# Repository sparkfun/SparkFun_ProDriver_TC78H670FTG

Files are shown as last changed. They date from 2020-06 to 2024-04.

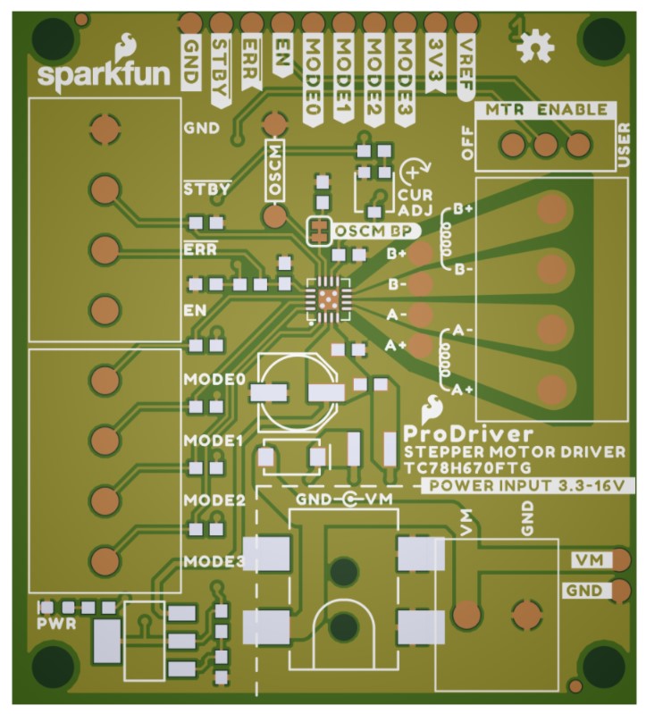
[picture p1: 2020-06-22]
Documents/brd_top_preivew.jpg

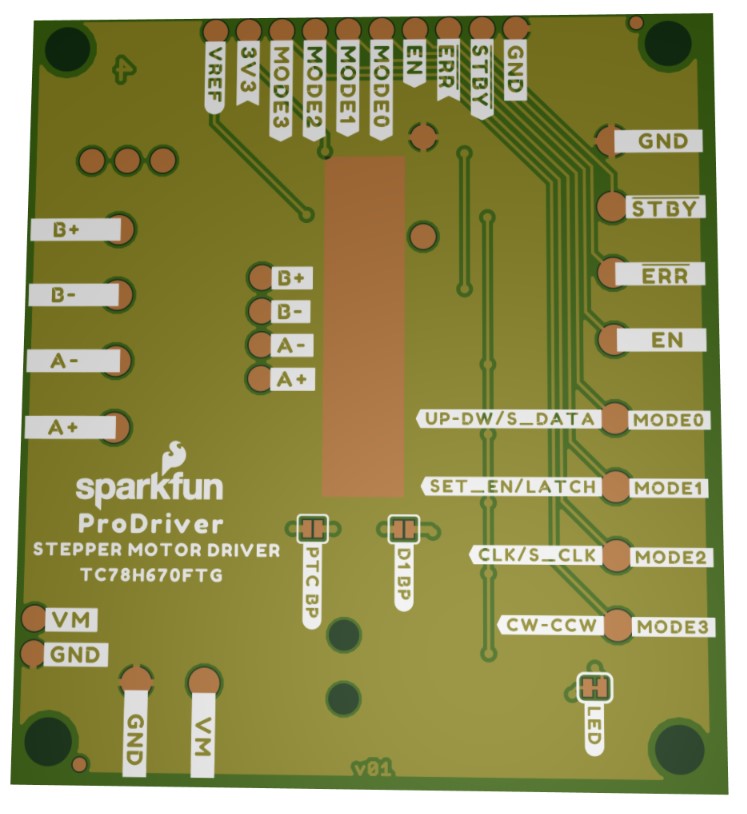
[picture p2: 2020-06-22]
Documents/brd_bottom_preivew.jpg

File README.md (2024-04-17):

SparkFun ProDriver - Stepper Motor Driver (TC78H670FTG)
========================================

SparkFun ProDriver - Stepper Motor Driver (TC78H670FTG)

[*SparkFun ProDriver - Stepper Motor Driver (TC78H670FTG) (ROB-16836)*](https://www.sparkfun.com/products/16836)

The SparkFun ProDriver makes it easy to start developing with the TC78H670FTG bipolar stepper motor driver from Toshiba! Latch terminals provide instant solder-less connections to every feature offered. Use our extensive Arduino Library with 10 examples, and you can quickly explore the many features of this precise and small package size motor driver IC.

In addition to high resolution control (down to 1/128th of a step), the ProDriver can be controlled via traditional clock-in stepping or serial commands. Both methods are demonstrated in the Arduino Library. The serial command method is especially unique in that it allows the user to precisely control the phase, torque, current limit and mixed decay ratio of each coil immediately during stepping. Most stepper motor driver ICs require using an external trimpot to set the current limit, but with the ProDriver, you can precisely adjust this via serial commands!

Repository Contents
-------------------

* **/Documentation** - Datasheets, additional product information
* **/Hardware** - Eagle design files (.brd, .sch)
* **/Hardware/Production** - Production panel files and gerbers (.brd)

Documentation
--------------

* **[Hookup Guide](https://learn.sparkfun.com/tutorials/1200)** - A hookup guide for the SparkFun ProDriver and Mini Stepper Motor Driver (TC78H670FTG)
* **[Arduino Library](https://github.com/sparkfun/SparkFun_ProDriver_TC78H670FTG_Arduino_Library)** - Basic Arduino Library for the SparkFun ProDriver and Mini Stepper Motor Driver (TC78H670FTG)

Product Variants
----------------
* SparkFun Mini Stepper Motor Driver - TC78H670FTG
  * [ROB-25167](https://www.sparkfun.com/products/25167)- v1.0, Initial Release
* SparkFun ProDriver - Stepper Motor Driver (TC78H670FTG)
  * [ROB-16836](https://www.sparkfun.com/products/16836)- v1.0, Initial Release

Product Versions
----------------
* [v01](https://github.com/sparkfun/SparkFun_ProDriver_TC78H670FTG/releases/tag/v10) - Initial Release

License Information
-------------------

This product is _**open source**_!

Please review the LICENSE.md file for license information.

If you have any questions or concerns on licensing, please contact technical support on our [SparkFun forums](https://forum.sparkfun.com/viewforum.php?f=152).

Distributed as-is; no warranty is given.

- Your friends at SparkFun.

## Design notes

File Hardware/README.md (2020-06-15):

SparkFun Particle Sensor MAX30101 (Qwiic) Design Files
=====================================

The .sch and .brd files hare are Eagle CAD schematic and PCB design files from SparkFun Electronics.
A freeware version of Eagle can be found [here](https://www.autodesk.com/products/eagle/free-download).

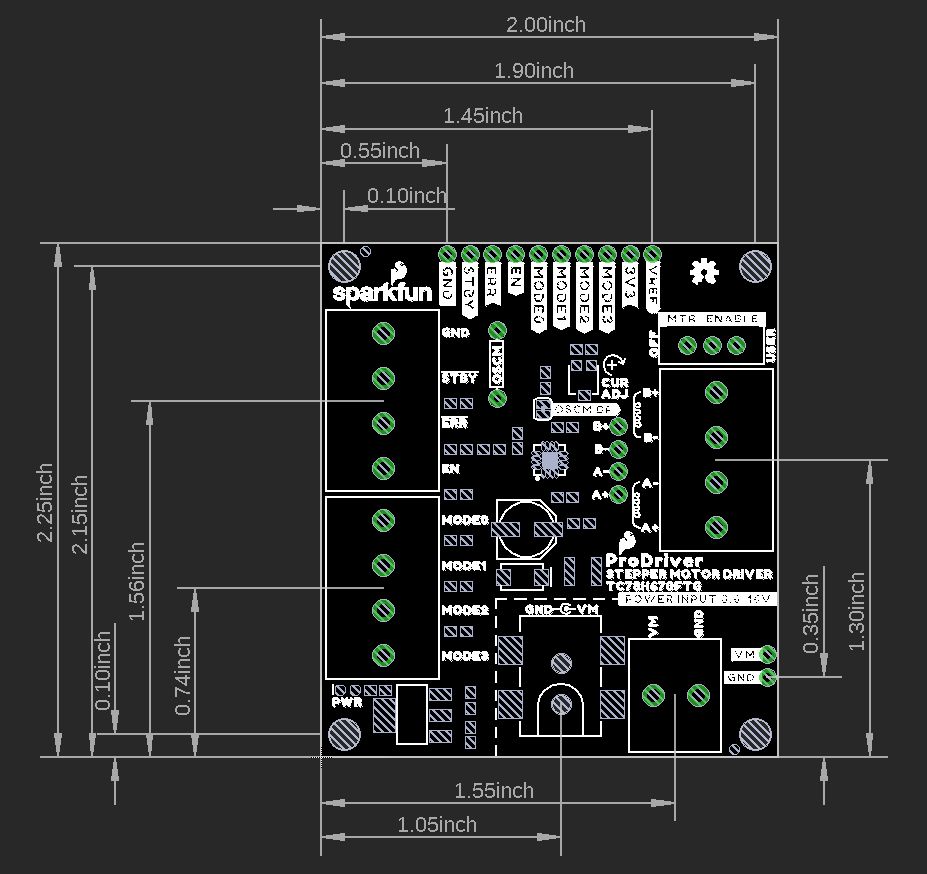
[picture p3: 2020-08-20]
Documents/SparkFun_ProDriver_DIMENSIONAL.png

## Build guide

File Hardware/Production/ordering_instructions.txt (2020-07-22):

panel size, 116x180mm
PCB thickness, 1.6mm
number of layers, 4
soldermask color, Red
silkscreen color, White
oz copper, 1oz
finish, HASL lead free
stencils, top+bottom
pcs per panel, 6
min trace width, 0.2032mm / 0.0080in
min drill size, 0.3048mm / 0.0120in
filename to layer stackup 1/2/3/4: GTL, GL2, GL3, GBL

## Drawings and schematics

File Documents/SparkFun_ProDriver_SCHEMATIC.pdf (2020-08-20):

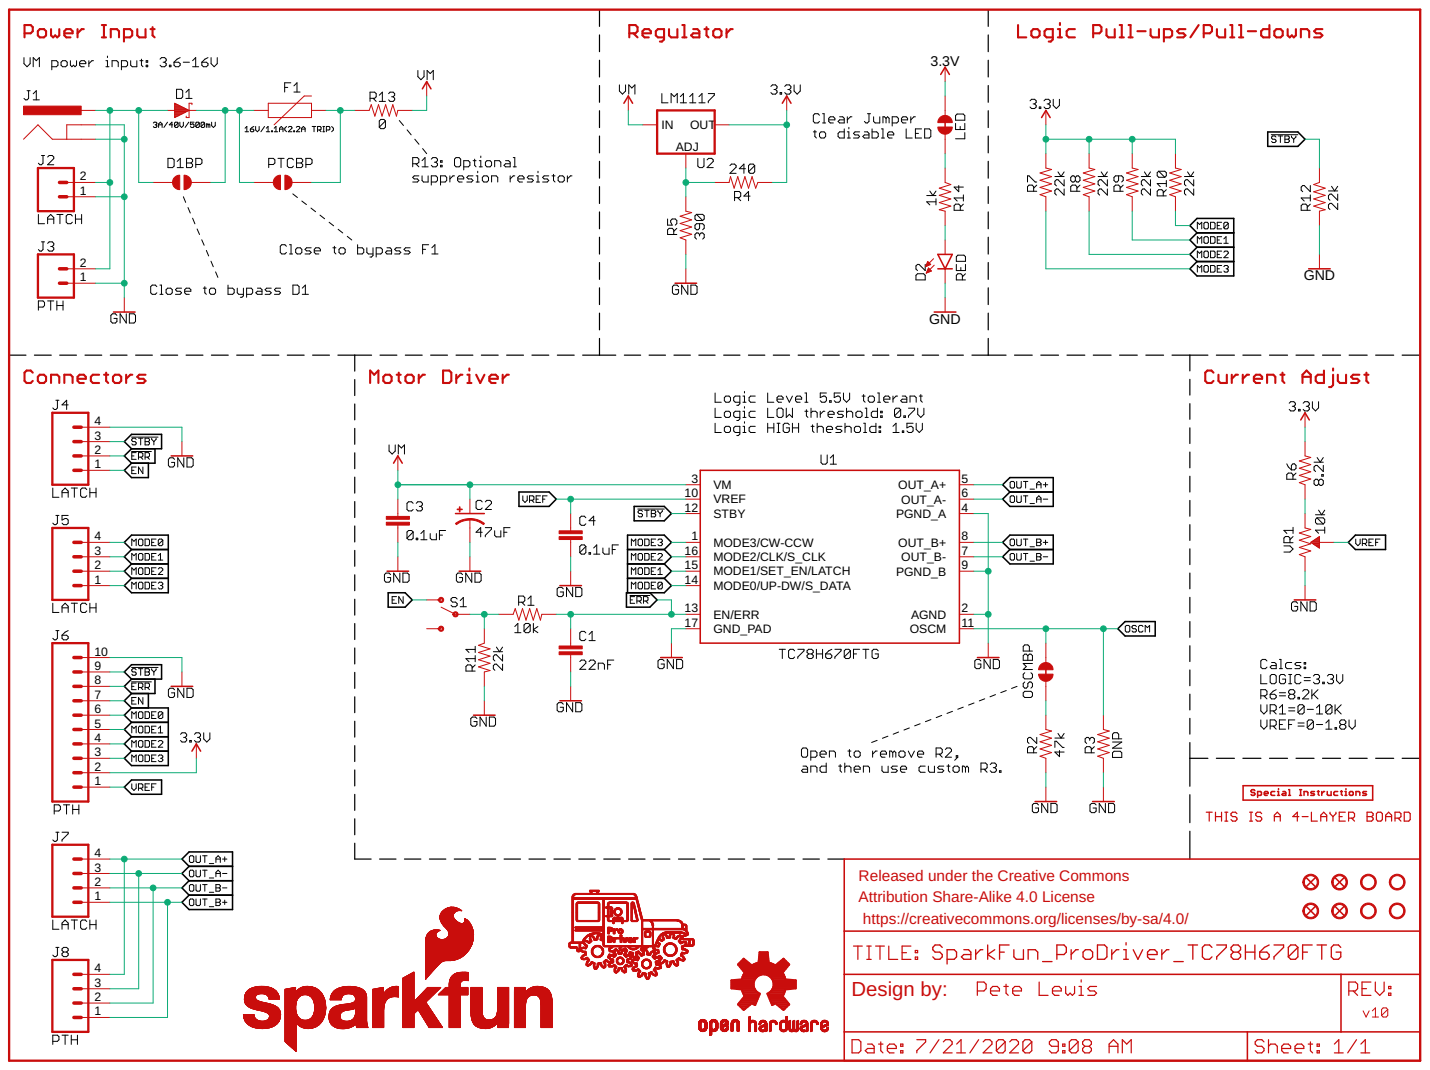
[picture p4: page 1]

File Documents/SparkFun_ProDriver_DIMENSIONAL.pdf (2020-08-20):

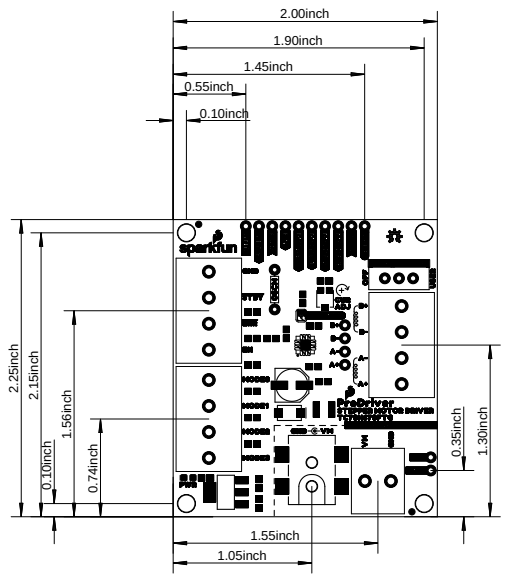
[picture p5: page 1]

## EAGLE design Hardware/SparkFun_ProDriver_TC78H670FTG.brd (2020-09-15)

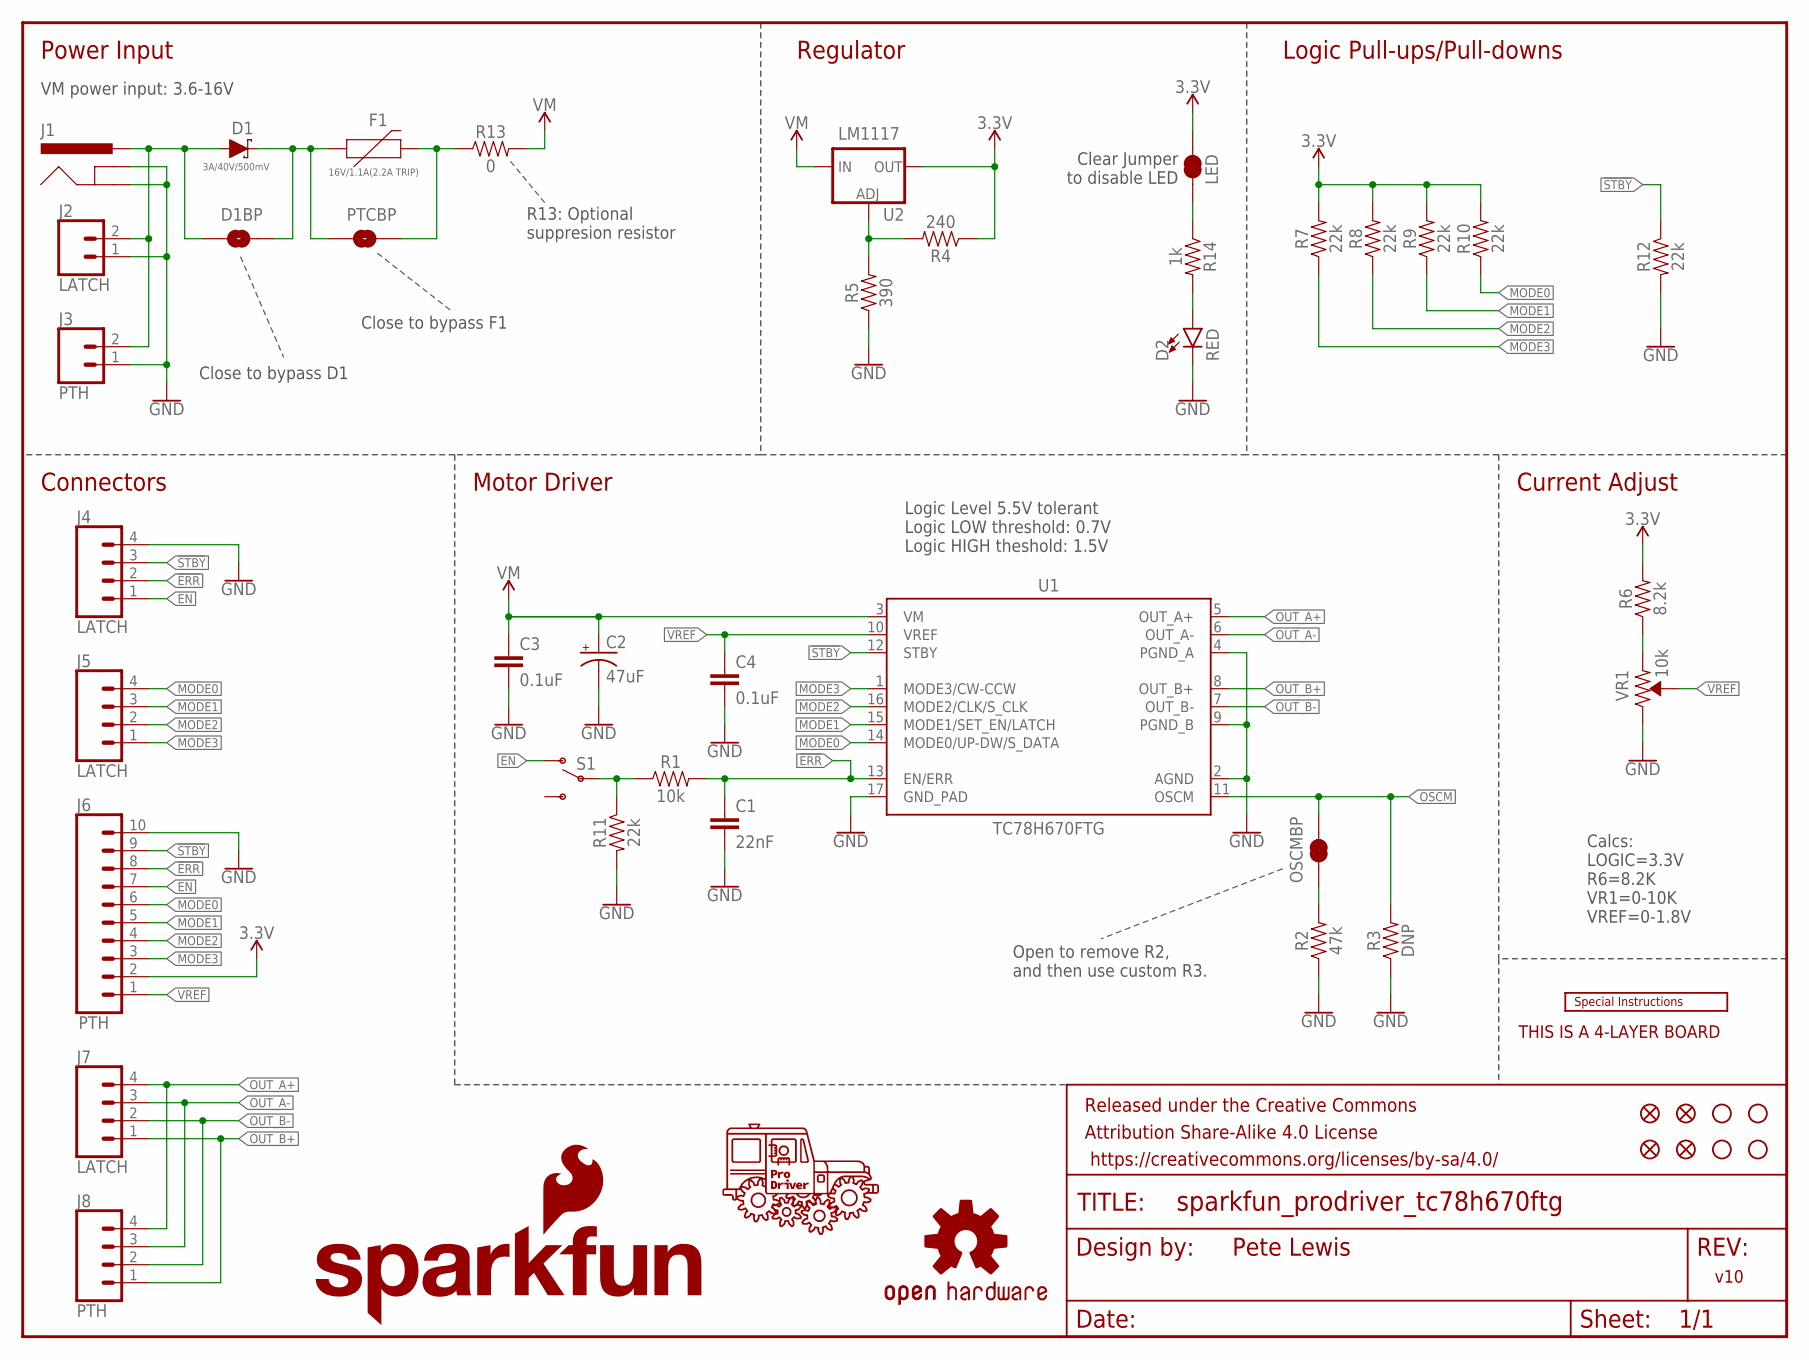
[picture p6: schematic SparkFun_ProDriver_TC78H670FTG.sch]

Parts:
C1: 22nF; 0603
C2: 47uF; PANASONIC_D
C3, C4: 0.1uF; 0603
D1: 3A/40V/500mV; SMA-DIODE
D1BP: JUMPER-SMT_2_NO_SILK; SMT-JUMPER_2_NO_SILK
D2: RED; LED-0603
F1: 16V/1.1A(2.2A TRIP); 1210
FID1, FID2, FID3, FID4: FIDUCIAL1X2; FIDUCIAL-1X2
FRAME1: FRAME-LETTER; CREATIVE_COMMONS
J1: POWER_JACKTOE; POWER_JACK_SMD_OVERPASTE_TOE
J2: LATCH; LATCHTERMINAL-5MM-2
J3: PTH; 1X02_NO_SILK
J4, J5, J7: LATCH; LATCHTERMINAL-5MM-4
J6: PTH; 1X10_NO_SILK
J8: PTH; 1X04_NO_SILK
JP4: LED; SMT-JUMPER_2_NC_TRACE_SILK
LOGO1: SFE_LOGO_NAME_FLAME.1_INCH; SFE_LOGO_NAME_FLAME_.1
LOGO2: OSHW-LOGOS; OSHW-LOGO-S
LOGO3: SPECIAL_INSTRUCTIONS-ORDERING; ORDERING_INSTRUCTIONS
OSCMBP: JUMPER-SMT_2_NC_TRACE_SILK; SMT-JUMPER_2_NC_TRACE_SILK
PTCBP: JUMPER-SMT_2_NO_SILK; SMT-JUMPER_2_NO_SILK
R1: 10k; 0603
R2: 47k; 0603
R3: DNP; AXIAL-0.3
R4: 240; 0603
R5: 390; 0603
R6: 8.2k; 0603
R7, R8, R9, R10, R11, R12: 22k; 0603
R13: 0; 0603
R14: 1k; 0603
S1: SWITCH-SPDT-PTH-11.6X4.0MM-LOCK; SWITCH_SPDT_PTH_11.6X4.0MM_LOCK
STANDOFF1, STANDOFF2, STANDOFF3, STANDOFF4: STAND-OFF
U1: TC78H670FTG; P-VQFN16-0303-0.50-001
U2: LM1117; SOT223
U$41: PRODRIVER_LOGO
VR1: 10k; TRIMPOT-SMD-3MM-CLOSED

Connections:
3.3V: J6.2, JP4.2, R4.1, R6.2, R7.2, R8.2, R9.2, R10.2, U2.2 (OUT), U2.4 (OUT)
!ERR: C1.1, J4.2, J6.8, R1.2, U1.13 (EN/ERR)
!STBY: J4.3, J6.9, R12.1, U1.12 (STBY)
EN: J4.1, J6.7, S1.1 (O)
GND: C1.2, C2.-, C3.2, C4.2, D2.C, J1.GND (GNDBREAK), J1.P$4 (GND), J2.1, J3.1, J4.4, J6.10, R2.1, R3.P$1 (1), R5.1, R11.2, R12.2, U1.2 (AGND), U1.4 (PGND_A), U1.9 (PGND_B), U1.17 (GND_PAD), VR1.3 (CW)
MODE0: J5.4, J6.6, R10.1, U1.14 (MODE0/UP-DW/S_DATA)
MODE1: J5.3, J6.5, R9.1, U1.15 (MODE1/SET_EN/LATCH)
MODE2: J5.2, J6.4, R8.1, U1.16 (MODE2/CLK/S_CLK)
MODE3: J5.1, J6.3, R7.1, U1.1 (MODE3/CW-CCW)
unnamed: D1.C, D1BP.2, F1.1, PTCBP.1
unnamed: OSCMBP.1, R2.2
unnamed: F1.2, PTCBP.2, R13.1
unnamed: R4.2, R5.2, U2.1 (ADJ)
unnamed: R6.1, VR1.1 (CCW)
unnamed: D2.A, R14.2
unnamed: R1.1, R11.1, S1.2
unnamed: JP4.1, R14.1
OSCM: OSCMBP.2, R3.P$2 (2), U1.11 (OSCM)
OUT_A+: J7.4, J8.4, U1.5 (OUT_A+)
OUT_A-: J7.3, J8.3, U1.6 (OUT_A-)
OUT_B+: J7.1, J8.1, U1.8 (OUT_B+)
OUT_B-: J7.2, J8.2, U1.7 (OUT_B-)
RAW: D1.A, D1BP.1, J1.VIN0 (PWR), J2.2, J3.2
VM: C2.+, C3.1, R13.2, U1.3 (VM), U2.3 (IN)
VREF: C4.1, J6.1, U1.10 (VREF), VR1.2 (WIPER)

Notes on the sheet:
v10
Pete Lewis
Power Input
Regulator
Logic Pull-ups/Pull-downs
Connectors
Motor Driver
Current Adjust
Open to remove R2, and then use custom R3.
Close to bypass F1
Close to bypass D1
R13: Optional suppresion resistor
Calcs: LOGIC=3.3V R6=8.2K VR1=0-10K VREF=0-1.8V
Clear Jumper to disable LED
VM power input: 3.6-16V
THIS IS A 4-LAYER BOARD
Logic Level 5.5V tolerant Logic LOW threshold: 0.7V Logic HIGH theshold: 1.5V

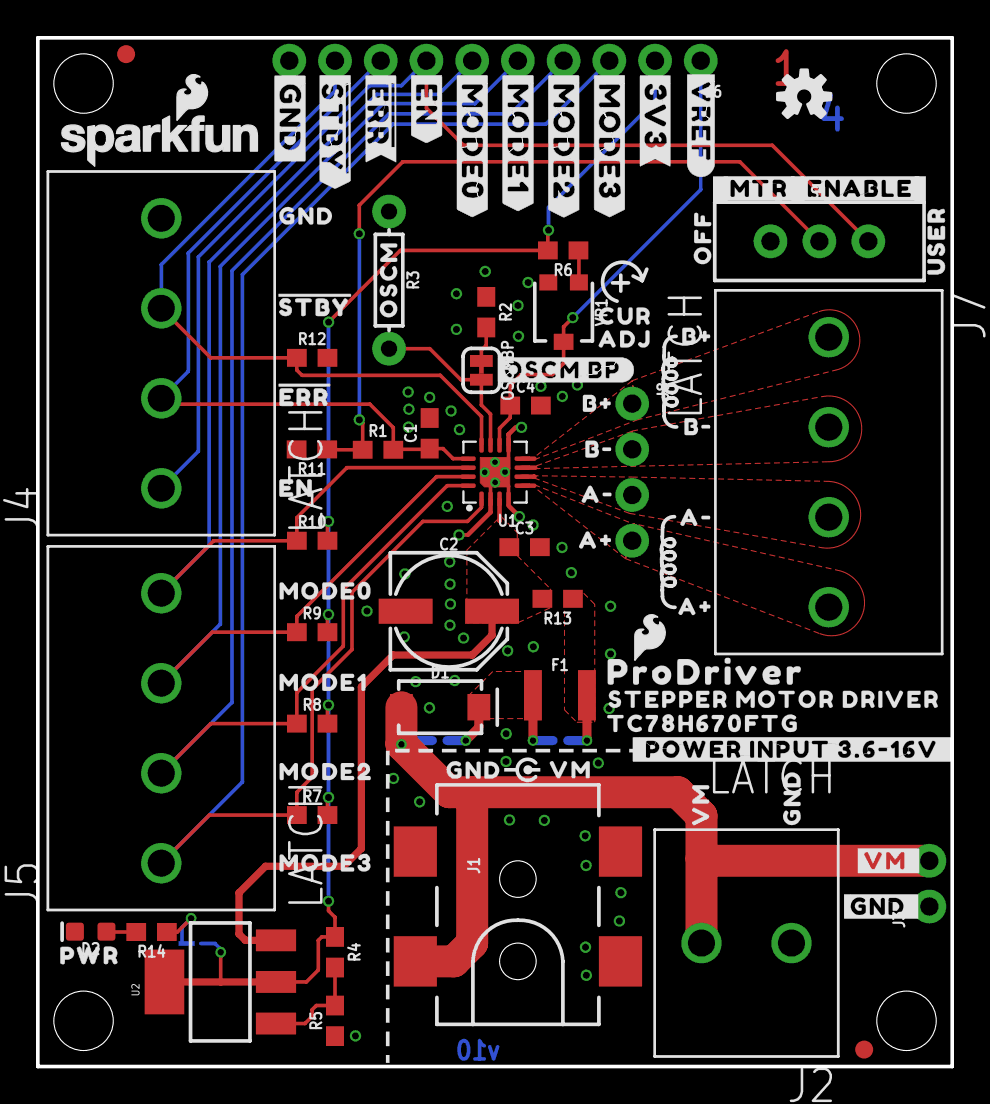
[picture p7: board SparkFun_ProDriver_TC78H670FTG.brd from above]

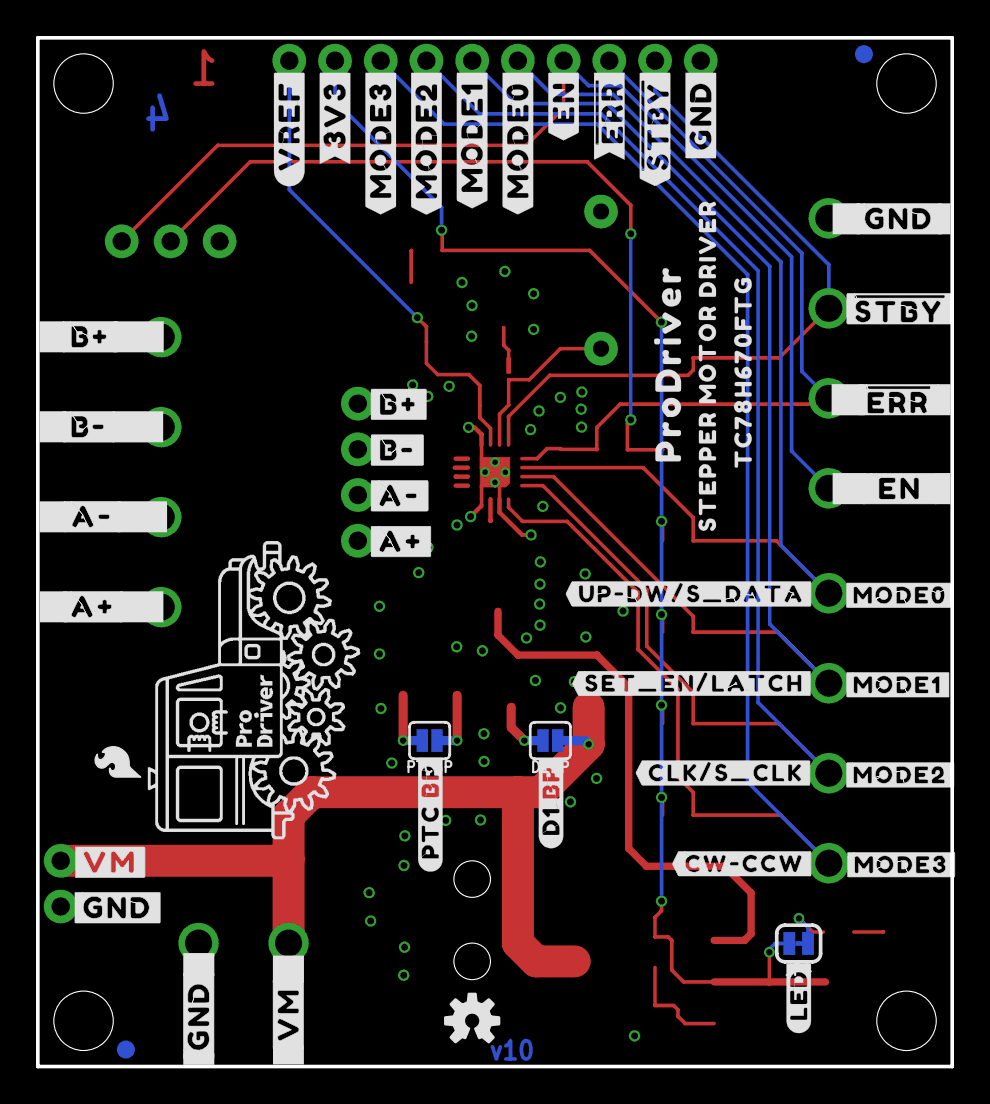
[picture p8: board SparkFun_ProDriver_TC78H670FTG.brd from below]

Board: 4 copper layers, 50.8 x 57.1 mm, 139 parts (48 on the bottom side), 25 nets.

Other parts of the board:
LOGO5: SFE_LOGO_NAME_FLAME.1_INCH; SFE_LOGO_FLAME_.1
LOGO6: SFE_LOGO_FLAME.1_INCH; SFE_LOGO_FLAME_.1
U$1, U$44: A#2
U$2, U$42: B#0
U$3, U$15: B#1
U$4, U$43: A#3
U$5, U$12, U$29: GND6
U$6, U$84: TC78H670FTG0
U$7: USER0
U$8: #ERR#3
U$9, U$85: STEPPER_MOTOR_DRIVER0
U$10: CUR0
U$11, U$30: VM10
U$13: #EN#2
U$14: #MTR#0
U$16: #OSCM_BP#0
U$17: OFF0
U$18: OSCM0
U$19: EN0
U$20: ADJ0
U$21: #ENABLE#0
U$22: CURRENT_ADJUST
U$23: MODE30
U$24: MODE10
U$25: MODE20
U$26: MODE00
U$27: #GND_#0
U$28: #VM_#0
U$31, U$69, U$73: #GND#0
U$32: #VREF#0
U$33: #MODE0#4
U$34, U$35: ##ERR##5
U$36: #_POWER_INPUT_3#6#16V_#0
U$37, U$56: #B##0
U$38: #LED#10
U$40, U$86: PRODRIVER0
U$46: #MODE1#4
U$47: #MODE2#4
U$48: #MODE3#4
U$49, U$57: #B##1
U$50, U$58: #A##2
U$51, U$59: #A##3
U$52: #GND#5
U$53: ##STBY##1
U$54: ##STBY##7
U$55: #_EN_#0
U$60: #MODE0#0
U$61: #MODE1#0
U$62: #MODE2#0
U$63: #MODE3#0
U$64: #D1_BP#10
U$65: #CLK#S_CLK#0
U$66: #SET_EN#LATCH#0
U$67: #UP#DW#S_DATA#0
U$68, U$72: #VM#0
U$70: #PTC_BP#9
U$71: OSHW-LOGO-S
U$74: #MODE0#1
U$75, U$93: #3V3#4
U$80: #VREF#4
U$82: #CW#CCW#0
U$83: PWR0
U$87: ##STBY##0
U$89: #STBY#2
U$90: #MODE1#1
U$91: #MODE2#2
U$92: #MODE3#3
U$94: #EN#5
U$95: ##ERR##6
U$96: #GND#8

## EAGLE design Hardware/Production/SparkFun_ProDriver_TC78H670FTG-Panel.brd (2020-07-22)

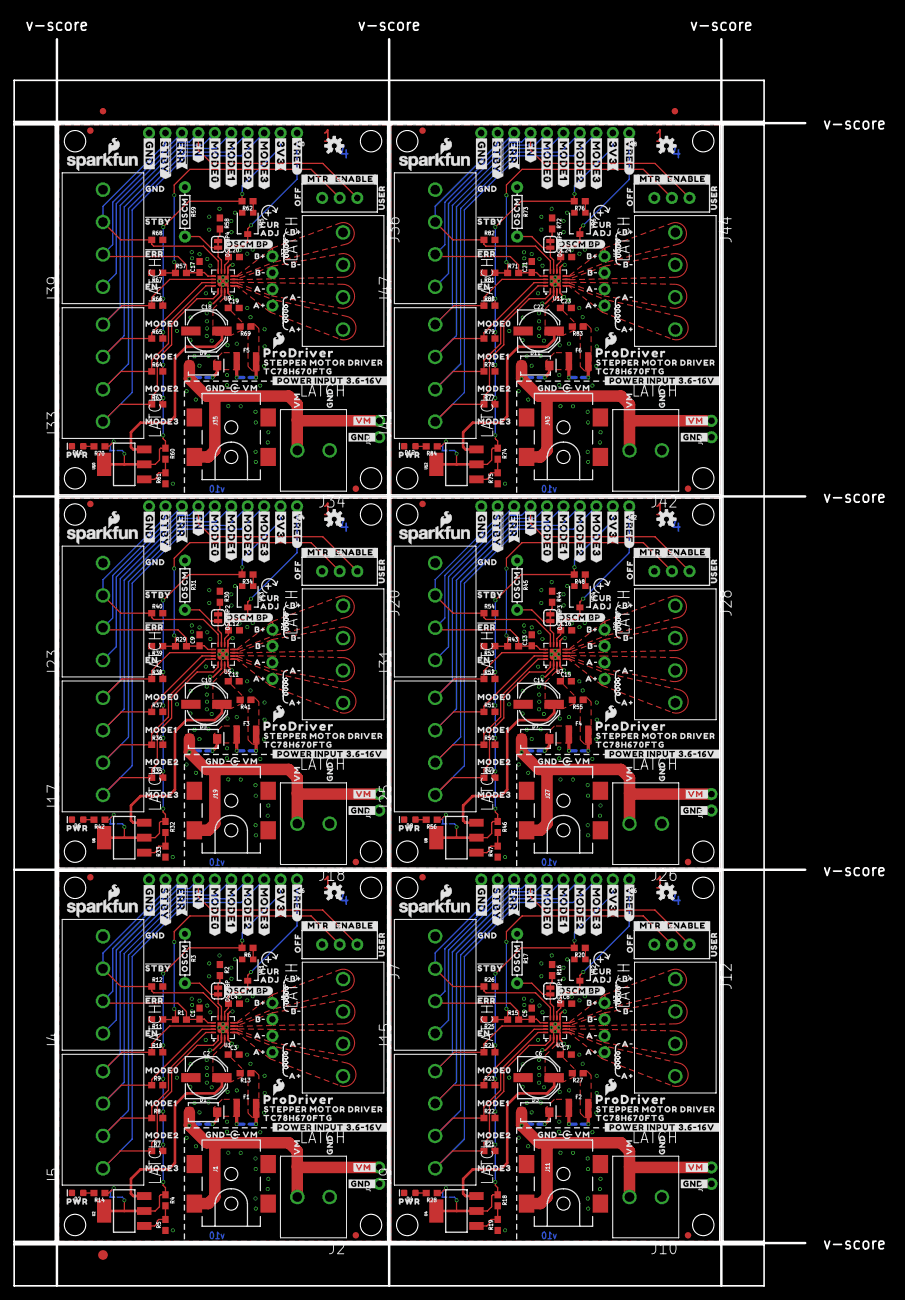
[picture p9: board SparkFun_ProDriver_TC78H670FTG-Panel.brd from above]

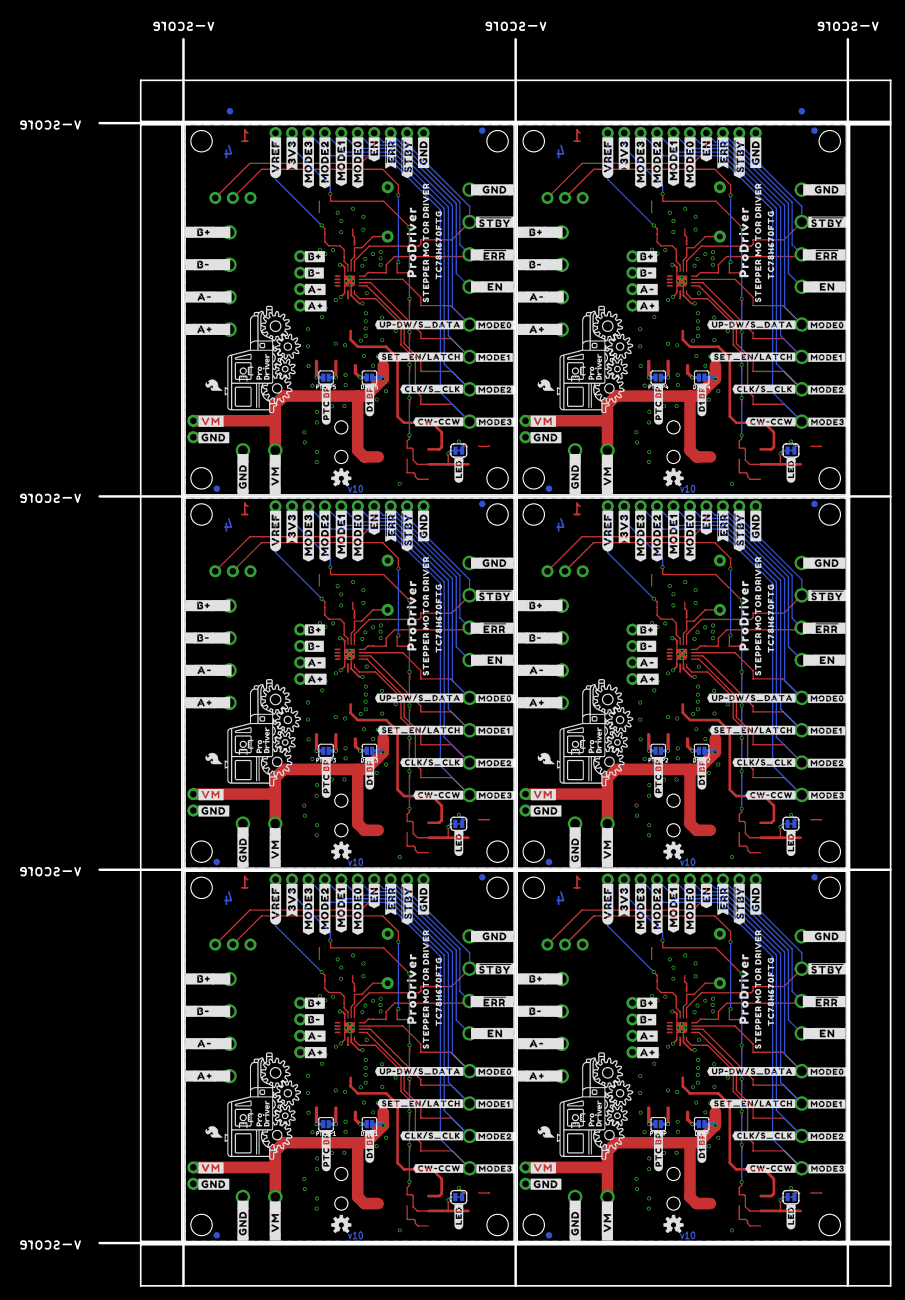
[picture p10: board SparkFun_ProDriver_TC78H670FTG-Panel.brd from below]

Board: 4 copper layers, 122.2 x 192.5 mm, 827 parts (290 on the bottom side), 150 nets.

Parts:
C1, C5, C9, C13, C17, C21: 22nF; 0603
C2, C6, C10, C14, C18, C22: 47uF; PANASONIC_D
C3, C4, C7, C8, C11, C12, C15, C16, C19, C20, C23, C24: 0.1uF; 0603
D1, D3, D5, D7, D9, D11: 3A/40V/500mV; SMA-DIODE
D1BP, D1BP1, D1BP2, D1BP3, D1BP4, D1BP5: SMT-JUMPER_2_NO_SILK
D2, D4, D6, D8, D10, D12: RED; LED-0603
E$1, E$2, E$3, E$4: FIDUCIAL-1X2
E$5: FIDUCIAL-1.5X3
F1, F2, F3, F4, F5, F6: 16V/1.1A(2.2A TRIP); 1210
FID1, FID2, FID3, FID4, FID5, FID6, FID7, FID8, FID9, FID10, FID11, FID12, FID13, FID14, FID15, FID16, FID17, FID18, FID19, FID20, FID21, FID22, FID23, FID24: FIDUCIAL1X2; FIDUCIAL-1X2
J1, J11, J19, J27, J35, J43: POWER_JACK_SMD_OVERPASTE_TOE
J2, J10, J18, J26, J34, J42: LATCH; LATCHTERMINAL-5MM-2
J3, J14, J22, J30, J38, J46: PTH; 1X02_NO_SILK
J4, J5, J7, J9, J12, J15, J17, J20, J23, J25, J28, J31, J33, J36, J39, J41, J44, J47: LATCH; LATCHTERMINAL-5MM-4
J6, J16, J24, J32, J40, J48: PTH; 1X10_NO_SILK
J8, J13, J21, J29, J37, J45: PTH; 1X04_NO_SILK
JP1, JP2, JP3, JP4, JP5, JP6: LED; SMT-JUMPER_2_NC_TRACE_SILK
LOGO1, LOGO3, LOGO9, LOGO13, LOGO17, LOGO21: SFE_LOGO_NAME_FLAME.1_INCH; SFE_LOGO_NAME_FLAME_.1
LOGO2, LOGO4, LOGO10, LOGO14, LOGO18, LOGO22: OSHW-LOGOS; OSHW-LOGO-S
LOGO5, LOGO7, LOGO11, LOGO15, LOGO19, LOGO23: SFE_LOGO_NAME_FLAME.1_INCH; SFE_LOGO_FLAME_.1
LOGO6, LOGO8, LOGO12, LOGO16, LOGO20, LOGO24: SFE_LOGO_FLAME.1_INCH; SFE_LOGO_FLAME_.1
OSCMBP, OSCMBP1, OSCMBP2, OSCMBP3, OSCMBP4, OSCMBP5: SMT-JUMPER_2_NC_TRACE_SILK
PTCBP, PTCBP1, PTCBP2, PTCBP3, PTCBP4, PTCBP5: SMT-JUMPER_2_NO_SILK
R1, R15, R29, R43, R57, R71: 10k; 0603
R2, R16, R30, R44, R58, R72: 47k; 0603
R3, R17, R31, R45, R59, R73: DNP; AXIAL-0.3
R4, R18, R32, R46, R60, R74: 240; 0603
R5, R19, R33, R47, R61, R75: 390; 0603
R6, R20, R34, R48, R62, R76: 8.2k; 0603
R7, R8, R9, R10, R11, R12, R21, R22, R23, R24, R25, R26, R35, R36, R37, R38, R39, R40, R49, R50, R51, R52, R53, R54, R63, R64, R65, R66, R67, R68, R77, R78, R79, R80, R81, R82: 22k; 0603
R13, R27, R41, R55, R69, R83: 0; 0603
R14, R28, R42, R56, R70, R84: 1k; 0603
S1, S2, S3, S4, S5, S6: SWITCH_SPDT_PTH_11.6X4.0MM_LOCK
STANDOFF1, STANDOFF2, STANDOFF3, STANDOFF4, STANDOFF5, STANDOFF6, STANDOFF7, STANDOFF8, STANDOFF9, STANDOFF10, STANDOFF11, STANDOFF12, STANDOFF13, STANDOFF14, STANDOFF15, STANDOFF16, STANDOFF17, STANDOFF18, STANDOFF19, STANDOFF20, STANDOFF21, STANDOFF22, STANDOFF23, STANDOFF24: STAND-OFF
U1, U3, U5, U7, U9, U11: TC78H670FTG; P-VQFN16-0303-0.50-001
U2, U4, U6, U8, U10, U12: LM1117; SOT223
U$1, U$44, U$76, U$118, U$179, U$206, U$267, U$294, U$355, U$382, U$443, U$470: A#2
U$2, U$39, U$42, U$116, U$177, U$204, U$265, U$292, U$353, U$380, U$441, U$468: B#0
U$3, U$15, U$45, U$115, U$178, U$203, U$266, U$291, U$354, U$379, U$442, U$467: B#1
U$4, U$43, U$77, U$117, U$180, U$205, U$268, U$293, U$356, U$381, U$444, U$469: A#3
U$5, U$12, U$29, U$78, U$81, U$107, U$181, U$183, U$195, U$269, U$271, U$283, U$357, U$359, U$371, U$445, U$447, U$459: GND6
U$6, U$84, U$109, U$149, U$197, U$237, U$285, U$325, U$373, U$413, U$461, U$501: TC78H670FTG0
U$7, U$157, U$245, U$333, U$421, U$509: USER0
U$8, U$155, U$243, U$331, U$419, U$507: #ERR#3
U$9, U$85, U$110, U$150, U$198, U$238, U$286, U$326, U$374, U$414, U$462, U$502: STEPPER_MOTOR_DRIVER0
U$10, U$98, U$186, U$274, U$362, U$450: CUR0
U$11, U$30, U$79, U$108, U$182, U$196, U$270, U$284, U$358, U$372, U$446, U$460: VM10
U$13, U$120, U$208, U$296, U$384, U$472: #EN#2
U$14, U$113, U$201, U$289, U$377, U$465: #MTR#0
U$16, U$158, U$246, U$334, U$422, U$510: #OSCM_BP#0
U$17, U$88, U$184, U$272, U$360, U$448: OFF0
U$18, U$97, U$185, U$273, U$361, U$449: OSCM0
U$19, U$119, U$207, U$295, U$383, U$471: EN0
U$20, U$99, U$187, U$275, U$363, U$451: ADJ0
U$21, U$114, U$202, U$290, U$378, U$466: #ENABLE#0
U$22, U$100, U$188, U$276, U$364, U$452: CURRENT_ADJUST
U$23, U$101, U$189, U$277, U$365, U$453: MODE30
U$24, U$102, U$190, U$278, U$366, U$454: MODE10
U$25, U$103, U$191, U$279, U$367, U$455: MODE20
U$26, U$104, U$192, U$280, U$368, U$456: MODE00
U$27, U$105, U$193, U$281, U$369, U$457: #GND_#0
U$28, U$106, U$194, U$282, U$370, U$458: #VM_#0
U$31, U$69, U$73, U$111, U$144, U$146, U$199, U$232, U$234, U$287, U$320, U$322, U$375, U$408, U$410, U$463, U$496, U$498: #GND#0
U$32, U$125, U$213, U$301, U$389, U$477: #VREF#0
U$33, U$121, U$209, U$297, U$385, U$473: #MODE0#4
U$34, U$35, U$156, U$175, U$244, U$263, U$332, U$351, U$420, U$439, U$508, U$527: ##ERR##5
U$36, U$176, U$264, U$352, U$440, U$528: #_POWER_INPUT_3#6#16V_#0
U$37, U$56, U$126, U$132, U$214, U$220, U$302, U$308, U$390, U$396, U$478, U$484: #B##0
U$38, U$173, U$261, U$349, U$437, U$525: #LED#10
U$40, U$86, U$112, U$151, U$200, U$239, U$288, U$327, U$376, U$415, U$464, U$503: PRODRIVER0
U$41, U$159, U$247, U$335, U$423, U$511: PRODRIVER_LOGO
U$46, U$122, U$210, U$298, U$386, U$474: #MODE1#4
U$47, U$123, U$211, U$299, U$387, U$475: #MODE2#4
U$48, U$124, U$212, U$300, U$388, U$476: #MODE3#4
U$49, U$57, U$127, U$133, U$215, U$221, U$303, U$309, U$391, U$397, U$479, U$485: #B##1
U$50, U$58, U$128, U$134, U$216, U$222, U$304, U$310, U$392, U$398, U$480, U$486: #A##2
U$51, U$59, U$129, U$135, U$217, U$223, U$305, U$311, U$393, U$399, U$481, U$487: #A##3
U$52, U$130, U$218, U$306, U$394, U$482: #GND#5
U$53, U$153, U$241, U$329, U$417, U$505: ##STBY##1
U$54, U$169, U$257, U$345, U$433, U$521: ##STBY##7
U$55, U$131, U$219, U$307, U$395, U$483: #_EN_#0
U$60, U$136, U$224, U$312, U$400, U$488: #MODE0#0
U$61, U$137, U$225, U$313, U$401, U$489: #MODE1#0
U$62, U$138, U$226, U$314, U$402, U$490: #MODE2#0
U$63, U$139, U$227, U$315, U$403, U$491: #MODE3#0
U$64, U$172, U$260, U$348, U$436, U$524: #D1_BP#10
U$65, U$140, U$228, U$316, U$404, U$492: #CLK#S_CLK#0
U$66, U$141, U$229, U$317, U$405, U$493: #SET_EN#LATCH#0
U$67, U$142, U$230, U$318, U$406, U$494: #UP#DW#S_DATA#0
U$68, U$72, U$143, U$145, U$231, U$233, U$319, U$321, U$407, U$409, U$495, U$497: #VM#0
U$70, U$171, U$259, U$347, U$435, U$523: #PTC_BP#9
U$71, U$160, U$248, U$336, U$424, U$512: OSHW-LOGO-S
U$74, U$161, U$249, U$337, U$425, U$513: #MODE0#1
U$75, U$93, U$165, U$174, U$253, U$262, U$341, U$350, U$429, U$438, U$517, U$526: #3V3#4
U$80, U$166, U$254, U$342, U$430, U$518: #VREF#4
U$82, U$147, U$235, U$323, U$411, U$499: #CW#CCW#0
U$83, U$148, U$236, U$324, U$412, U$500: PWR0
U$87, U$152, U$240, U$328, U$416, U$504: ##STBY##0
U$89, U$154, U$242, U$330, U$418, U$506: #STBY#2
U$90, U$162, U$250, U$338, U$426, U$514: #MODE1#1
U$91, U$163, U$251, U$339, U$427, U$515: #MODE2#2
U$92, U$164, U$252, U$340, U$428, U$516: #MODE3#3
U$94, U$167, U$255, U$343, U$431, U$519: #EN#5
U$95, U$168, U$256, U$344, U$432, U$520: ##ERR##6
U$96, U$170, U$258, U$346, U$434, U$522: #GND#8
VR1, VR2, VR3, VR4, VR5, VR6: 10k; TRIMPOT-SMD-3MM-CLOSED

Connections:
3.3V: J6.2, JP4.2, R4.1, R6.2, R7.2, R8.2, R9.2, R10.2, U2.2, U2.4
3.3V1: J16.2, JP1.2, R18.1, R20.2, R21.2, R22.2, R23.2, R24.2, U4.2, U4.4
3.3V2: J24.2, JP2.2, R32.1, R34.2, R35.2, R36.2, R37.2, R38.2, U6.2, U6.4
3.3V3: J32.2, JP3.2, R46.1, R48.2, R49.2, R50.2, R51.2, R52.2, U8.2, U8.4
3.3V4: J40.2, JP5.2, R60.1, R62.2, R63.2, R64.2, R65.2, R66.2, U10.2, U10.4
3.3V5: J48.2, JP6.2, R74.1, R76.2, R77.2, R78.2, R79.2, R80.2, U12.2, U12.4
!ERR: C1.1, J4.2, J6.8, R1.2, U1.13
!ERR1: C5.1, J15.2, J16.8, R15.2, U3.13
!ERR2: C9.1, J23.2, J24.8, R29.2, U5.13
!ERR3: C13.1, J31.2, J32.8, R43.2, U7.13
!ERR4: C17.1, J39.2, J40.8, R57.2, U9.13
!ERR5: C21.1, J47.2, J48.8, R71.2, U11.13
!STBY: J4.3, J6.9, R12.1, U1.12
!STBY1: J15.3, J16.9, R26.1, U3.12
!STBY2: J23.3, J24.9, R40.1, U5.12
!STBY3: J31.3, J32.9, R54.1, U7.12
!STBY4: J39.3, J40.9, R68.1, U9.12
!STBY5: J47.3, J48.9, R82.1, U11.12
EN: J4.1, J6.7, S1.1
EN1: J15.1, J16.7, S2.1
EN2: J23.1, J24.7, S3.1
EN3: J31.1, J32.7, S4.1
EN4: J39.1, J40.7, S5.1
EN5: J47.1, J48.7, S6.1
GND: C1.2, C2.-, C3.2, C4.2, D2.C, J1.GND, J1.P$4, J2.1, J3.1, J4.4, J6.10, R2.1, R3.P$1, R5.1, R11.2, R12.2, U1.2, U1.4, U1.9, U1.17, VR1.3
GND1: C5.2, C6.-, C7.2, C8.2, D4.C, J10.1, J11.GND, J11.P$4, J14.1, J15.4, J16.10, R16.1, R17.P$1, R19.1, R25.2, R26.2, U3.2, U3.4, U3.9, U3.17, VR2.3
GND2: C9.2, C10.-, C11.2, C12.2, D6.C, J18.1, J19.GND, J19.P$4, J22.1, J23.4, J24.10, R30.1, R31.P$1, R33.1, R39.2, R40.2, U5.2, U5.4, U5.9, U5.17, VR3.3
GND3: C13.2, C14.-, C15.2, C16.2, D8.C, J26.1, J27.GND, J27.P$4, J30.1, J31.4, J32.10, R44.1, R45.P$1, R47.1, R53.2, R54.2, U7.2, U7.4, U7.9, U7.17, VR4.3
GND4: C17.2, C18.-, C19.2, C20.2, D10.C, J34.1, J35.GND, J35.P$4, J38.1, J39.4, J40.10, R58.1, R59.P$1, R61.1, R67.2, R68.2, U9.2, U9.4, U9.9, U9.17, VR5.3
GND5: C21.2, C22.-, C23.2, C24.2, D12.C, J42.1, J43.GND, J43.P$4, J46.1, J47.4, J48.10, R72.1, R73.P$1, R75.1, R81.2, R82.2, U11.2, U11.4, U11.9, U11.17, VR6.3
MODE0: J5.4, J6.6, R10.1, U1.14
MODE1: J5.3, J6.5, R9.1, U1.15
MODE2: J5.2, J6.4, R8.1, U1.16
MODE3: J5.1, J6.3, R7.1, U1.1
MODE4: J9.1, J16.3, R21.1, U3.1
MODE5: J9.2, J16.4, R22.1, U3.16
MODE6: J9.3, J16.5, R23.1, U3.15
MODE7: J9.4, J16.6, R24.1, U3.14
MODE8: J17.1, J24.3, R35.1, U5.1
MODE9: J17.2, J24.4, R36.1, U5.16
MODE10: J17.3, J24.5, R37.1, U5.15
MODE11: J17.4, J24.6, R38.1, U5.14
MODE12: J25.1, J32.3, R49.1, U7.1
MODE13: J25.2, J32.4, R50.1, U7.16
MODE14: J25.3, J32.5, R51.1, U7.15
MODE15: J25.4, J32.6, R52.1, U7.14
MODE16: J33.1, J40.3, R63.1, U9.1
MODE17: J33.2, J40.4, R64.1, U9.16
MODE18: J33.3, J40.5, R65.1, U9.15
MODE19: J33.4, J40.6, R66.1, U9.14
MODE20: J41.1, J48.3, R77.1, U11.1
MODE21: J41.2, J48.4, R78.1, U11.16
MODE22: J41.3, J48.5, R79.1, U11.15
MODE23: J41.4, J48.6, R80.1, U11.14
unnamed: D1.C, D1BP.2, F1.1, PTCBP.1
unnamed: OSCMBP.1, R2.2
unnamed: F1.2, PTCBP.2, R13.1
unnamed: R4.2, R5.2, U2.1
unnamed: R6.1, VR1.1
unnamed: D2.A, R14.2
unnamed: R1.1, R11.1, S1.2
unnamed: JP4.1, R14.1
unnamed: OSCMBP1.1, R16.2
unnamed: R18.2, R19.2, U4.1
unnamed: R20.1, VR2.1
unnamed: D1BP1.2, D3.C, F2.1, PTCBP1.1
unnamed: F2.2, PTCBP1.2, R27.1
unnamed: D4.A, R28.2
unnamed: JP1.1, R28.1
unnamed: R15.1, R25.1, S2.2
unnamed: OSCMBP2.1, R30.2
unnamed: R32.2, R33.2, U6.1
unnamed: R34.1, VR3.1
unnamed: D1BP2.2, D5.C, F3.1, PTCBP2.1
unnamed: F3.2, PTCBP2.2, R41.1
unnamed: D6.A, R42.2
unnamed: JP2.1, R42.1
unnamed: R29.1, R39.1, S3.2
unnamed: OSCMBP3.1, R44.2
unnamed: R46.2, R47.2, U8.1
unnamed: R48.1, VR4.1
unnamed: D1BP3.2, D7.C, F4.1, PTCBP3.1
unnamed: F4.2, PTCBP3.2, R55.1
unnamed: D8.A, R56.2
unnamed: JP3.1, R56.1
unnamed: R43.1, R53.1, S4.2
unnamed: OSCMBP4.1, R58.2
unnamed: R60.2, R61.2, U10.1
unnamed: R62.1, VR5.1
unnamed: D1BP4.2, D9.C, F5.1, PTCBP4.1
unnamed: F5.2, PTCBP4.2, R69.1
unnamed: D10.A, R70.2
unnamed: JP5.1, R70.1
unnamed: R57.1, R67.1, S5.2
unnamed: OSCMBP5.1, R72.2
unnamed: R74.2, R75.2, U12.1
unnamed: R76.1, VR6.1
unnamed: D1BP5.2, D11.C, F6.1, PTCBP5.1
unnamed: F6.2, PTCBP5.2, R83.1
unnamed: D12.A, R84.2
unnamed: JP6.1, R84.1
unnamed: R71.1, R81.1, S6.2
OSCM: OSCMBP.2, R3.P$2, U1.11
OSCM1: OSCMBP1.2, R17.P$2, U3.11
OSCM2: OSCMBP2.2, R31.P$2, U5.11
OSCM3: OSCMBP3.2, R45.P$2, U7.11
OSCM4: OSCMBP4.2, R59.P$2, U9.11
OSCM5: OSCMBP5.2, R73.P$2, U11.11
OUT_A+: J7.4, J8.4, U1.5
OUT_A+1: J12.4, J13.4, U3.5
OUT_A+2: J20.4, J21.4, U5.5
OUT_A+3: J28.4, J29.4, U7.5
OUT_A+4: J36.4, J37.4, U9.5
OUT_A+5: J44.4, J45.4, U11.5
OUT_A-: J7.3, J8.3, U1.6
OUT_A-1: J12.3, J13.3, U3.6
OUT_A-2: J20.3, J21.3, U5.6
OUT_A-3: J28.3, J29.3, U7.6
OUT_A-4: J36.3, J37.3, U9.6
OUT_A-5: J44.3, J45.3, U11.6
OUT_B+: J7.1, J8.1, U1.8
OUT_B+1: J12.1, J13.1, U3.8
OUT_B+2: J20.1, J21.1, U5.8
OUT_B+3: J28.1, J29.1, U7.8
OUT_B+4: J36.1, J37.1, U9.8
OUT_B+5: J44.1, J45.1, U11.8
OUT_B-: J7.2, J8.2, U1.7
OUT_B-1: J12.2, J13.2, U3.7
OUT_B-2: J20.2, J21.2, U5.7
OUT_B-3: J28.2, J29.2, U7.7
OUT_B-4: J36.2, J37.2, U9.7
OUT_B-5: J44.2, J45.2, U11.7
RAW: D1.A, D1BP.1, J1.VIN0, J2.2, J3.2
RAW1: D1BP1.1, D3.A, J10.2, J11.VIN0, J14.2
RAW2: D1BP2.1, D5.A, J18.2, J19.VIN0, J22.2
RAW3: D1BP3.1, D7.A, J26.2, J27.VIN0, J30.2
RAW4: D1BP4.1, D9.A, J34.2, J35.VIN0, J38.2
RAW5: D1BP5.1, D11.A, J42.2, J43.VIN0, J46.2
VM: C2.+, C3.1, R13.2, U1.3, U2.3
VM1: C6.+, C7.1, R27.2, U3.3, U4.3
VM2: C10.+, C11.1, R41.2, U5.3, U6.3
VM3: C14.+, C15.1, R55.2, U7.3, U8.3
VM4: C18.+, C19.1, R69.2, U9.3, U10.3
VM5: C22.+, C23.1, R83.2, U11.3, U12.3
VREF: C4.1, J6.1, U1.10, VR1.2
VREF1: C8.1, J16.1, U3.10, VR2.2
VREF2: C12.1, J24.1, U5.10, VR3.2
VREF3: C16.1, J32.1, U7.10, VR4.2
VREF4: C20.1, J40.1, U9.10, VR5.2
VREF5: C24.1, J48.1, U11.10, VR6.2

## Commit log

2020-06-15 layout coming along start to lay traces
    polygon crashed eagle, so i figured i better start commiting
    [SparkFun_TC78H670FTG_Breakout.brd, SparkFun_TC78H670FTG_Breakout.sch]
2020-06-15 update file name to correct product name
    [SparkFun_ProDriver_TC78H670FTG.brd, SparkFun_ProDriver_TC78H670FTG.sch]
2020-06-15 layout almost done still need to add bstop for heatsink
    [SparkFun_ProDriver_TC78H670FTG.brd]
2020-06-15 nudged OSCM res away, added bstop for heatsink
    [SparkFun_ProDriver_TC78H670FTG.brd, SparkFun_ProDriver_TC78H670FTG.sch]
2020-06-16 Corrected EN/ERR pin access
    [SparkFun_ProDriver_TC78H670FTG.brd, SparkFun_ProDriver_TC78H670FTG.sch]
2020-06-16 small sch nudge cleanup
    [SparkFun_ProDriver_TC78H670FTG.sch]
2020-06-17 nudged 1x4 latch terminals apart to avoid part collision
    [SparkFun_ProDriver_TC78H670FTG.brd]
2020-06-17 moved connectors inward to allow for depanel blade space
    Also added tcream to IC package
    [SparkFun_ProDriver_TC78H670FTG.brd, SparkFun_ProDriver_TC78H670FTG.sch]
2020-06-17 Added PTC and 0Ohm res to power input
    plus bypass jumpers down below
    [SparkFun_ProDriver_TC78H670FTG.brd, SparkFun_ProDriver_TC78H670FTG.sch]
2020-06-17 added value to lm1117 so it's visible in sch
    [SparkFun_ProDriver_TC78H670FTG.brd, SparkFun_ProDriver_TC78H670FTG.sch]
2020-06-17 bplace labels done
    [SparkFun_ProDriver_TC78H670FTG.brd]
2020-06-18 rotated GND/VM bottom labels to read same direction as others
    [SparkFun_ProDriver_TC78H670FTG.brd]
2020-06-18 first run of checklist catches (pre-design review)
    -4-layer board warnings in sch, brd, plus 1,2,3,4 in coppers
    -added power LED
    -added specail ordering instructions for 4-layer and 2 oz copper
    -added measures
    -ERR and STBY labels show active low overline now
    [SparkFun_ProDriver_TC78H670FTG.brd, SparkFun_ProDriver_TC78H670FTG.sch]
2020-06-19 ERR and STBY NET names to active low - now with overline
    [SparkFun_ProDriver_TC78H670FTG.brd, SparkFun_ProDriver_TC78H670FTG.sch]
2020-06-19 Moved to pull-downs on EN and STBY
    Because the powerup sequence requires that EN and STBY be low (while VM comes up), we should default these to low. Then the user can wire up these lines to their micro and write them HIGH when necessary.
    -Adjusted how the enable hardware slide switch works. Now it simply disconnects the "user" control, so that it lets the pull-down resistor take effect. In this way, it will overide any logic level the user has provided on EN.
    -Changes enable switch silk label to "user" indicating that the user must now provide logic control on the latch terminals or PTH headers.
    -Added note in schematic about logic level tolerances
    -re routed and moves some traces to mainta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
    [SparkFun_ProDriver_TC78H670FTG.brd, SparkFun_ProDriver_TC78H670FTG.sch]
2020-06-19 Suggestions from design review
    -Jumper names same in sch and brd labels
    -JP1 to OSCM
    -ERR net position aligned with others
    -changed power input silk to 3.3V-16V, also updated sch
    -added more vias near IC, head sink exposed copper, and VM input traces to help heat transfer to inner layers.
    [SparkFun_ProDriver_TC78H670FTG.brd, SparkFun_ProDriver_TC78H670FTG.sch]
2020-06-22 Double-check fixes
    -Eagle Library had storefront SKUs for latch terminals. Corrected to prod IDs.
    -removed unnecessary flame symbol in sch (lcopied a second footprint to keep in board).
    -text font to vector on one sch paragraph
    [SparkFun_ProDriver_TC78H670FTG.brd, SparkFun_ProDriver_TC78H670FTG.sch]
2020-06-22 added dummy traces to 2/15, removed bottom paste on IC package
    -Added some dummy traces to 2/15 inner layers so the CAMmer tool will pick up on them and create gerbers.
    -There was some bottom paste on the IC footprint I never noticed till reviewing gerbers, I think this was left over from the QFN footprint I started from.
    -Also updated preview jpgs to reflect most recent design.
    [SparkFun_ProDriver_TC78H670FTG.brd, SparkFun_ProDriver_TC78H670FTG.sch]
2020-06-22 production files - also decided to go with 1 OZ copper
    -panelized for proto panel order 2x2
    -removed "2OZ Copper" note from special ordering instructions. Fab house for protos (JLC) has huge price jump for 2 OZ, so gonna try 1 OZ for protos and see how heat sinking does.
    -adjusted ordering instrutions text file to reflext black soldermask
    [SparkFun_ProDriver_TC78H670FTG-Panel.GBL, SparkFun_ProDriver_TC78H670FTG-Panel.GBO, SparkFun_ProDriver_TC78H670FTG-Panel.GBP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]
2020-07-08 Added new jeep pro driver logo to bottom silk
    [SparkFun_ProDriver_TC78H670FTG.brd, SparkFun_ProDriver_TC78H670FTG.sch]
2020-07-17 Rotated bottom silk labels to match product name/logo
    also updated version number to v10 in brd bottom copper and sch
    [SparkFun_ProDriver_TC78H670FTG.brd, SparkFun_ProDriver_TC78H670FTG.sch]
2020-07-20 Post design reveiew (REDs)
    -Moved R3 (OSCM) away from exposed bottom copper (for the optional heat sink). This is nice to add a little extra clarance in case you want to use a larger heatsink.
    [SparkFun_ProDriver_TC78H670FTG.brd]
2020-07-21 Corrected input voltage range to 3.6-16V on sch and brd
    [SparkFun_ProDriver_TC78H670FTG.brd, SparkFun_ProDriver_TC78H670FTG.sch]
2020-07-22 Production files for v10
    [SparkFun_ProDriver_TC78H670FTG-Panel.GBL, SparkFun_ProDriver_TC78H670FTG-Panel.GBO, SparkFun_ProDriver_TC78H670FTG-Panel.GBS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]
2020-08-21 Update SparkFun_ProDriver_TC78H670FTG.brd
    Added dimensions for the latch pin component widths and the enable switch location on the measurements layer
    [SparkFun_ProDriver_TC78H670FTG.brd]
2020-09-15 Replaced IC device to use sparkfun eagle library
    [SparkFun_ProDriver_TC78H670FTG.brd, SparkFun_ProDriver_TC78H670FTG.sch]
2024-04-17 Update LICENSE.md
    Remove carriage returns
    Fix grammar
2024-04-17 Updates for the Mini Stepper Motor Driver

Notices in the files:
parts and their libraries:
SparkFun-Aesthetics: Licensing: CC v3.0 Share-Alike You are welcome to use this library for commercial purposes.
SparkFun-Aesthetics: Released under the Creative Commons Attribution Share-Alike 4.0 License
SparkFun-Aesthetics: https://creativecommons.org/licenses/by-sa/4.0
